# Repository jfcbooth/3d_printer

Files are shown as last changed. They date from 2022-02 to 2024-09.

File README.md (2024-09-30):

# 3D PEEK Printer

All the project files are in the directories above. The graphic below sums up the project. If you are curious about how something was implemented, read the [final report here](reports/Capstone_Final_Report.pdf). I recommend first skimming it and looking at the images for a better idea of what the project entailed.

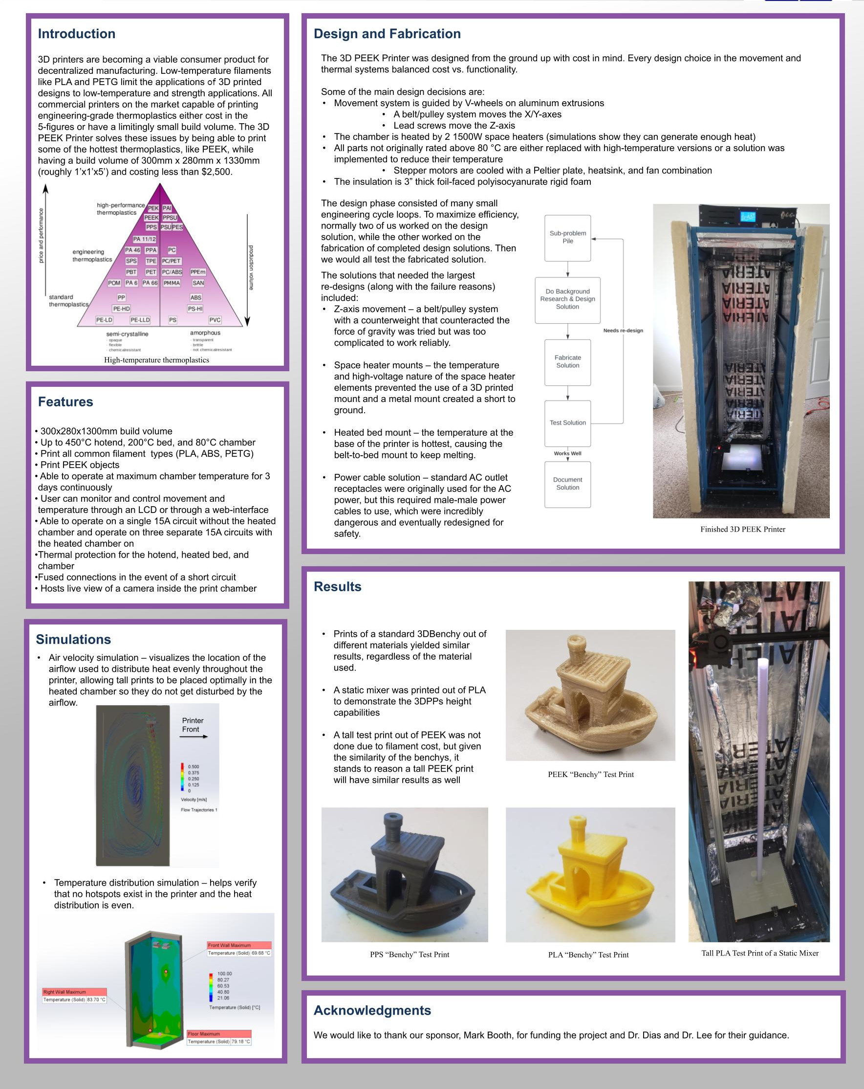
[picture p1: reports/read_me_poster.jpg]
Poster


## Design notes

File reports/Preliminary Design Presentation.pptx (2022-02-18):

## 3D Peek Printer

- Senior Capstone Design

## 3D Printing Technology

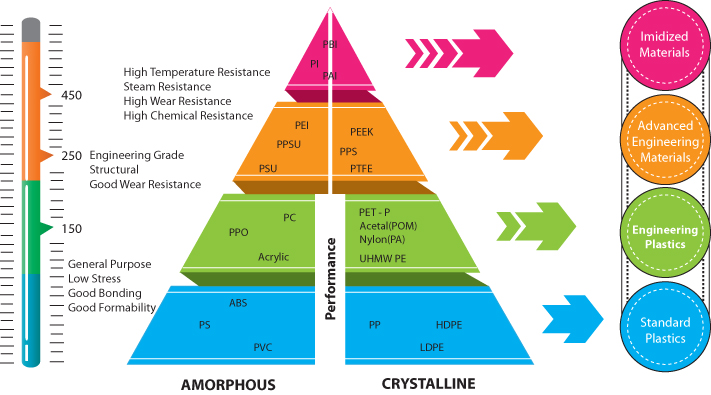
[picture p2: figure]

Source: https://www.cil.co.th/engineering-plastics/

- Pros
  - Low machine cost
  - Low per-unit print cost
  - Rapid Production
  - Low size footprint
  - Wide availability
- Cons
  - Dimensionally inaccurate
    - ±0.1mm vs ±0.005mm for CNC
  - Limited object size
  - Low strength
  - Low temperature

## Market Analysis

| Max Extruder Temp. (°C) | Max Bed Temp. (°C) | Max Chamber Temp. (°C) | Build Volume (mm³) | Price ($)
Average Commercial PEEK Printer | 490 | 193 | 165 | 5.01e7 | 61,000
Intamsys Funmat HT | 450 | 160 | 90 | 1.76e7 | 6,000
Aon-M2+ | 450 | 200 | 135 | 1.30e8 | 50,000
3DPP | 450 | 200 | 80 | 1.12e8 | 2,500

- Intamsys Funmat HT
  - 10x smaller build volume
  - Double price

- Aon-M2+
  - Similar build volume
  - 20x price

## Design Requirements

Functional Requirements
- Respond to movement commands in the X, Y, Z, and extruder directions
- Heat nozzle to 450 °C, bed to 200 °C, chamber to 80 °C
- Print all common filament types without heated chamber
- Can print PEEK/PSU object
- Print volume of 300x280x1330mm
- Operate at maximum chamber temperature for 3 days continuously
Usability Requirements
- System can operate on a local 20A breaker without heated chamber and with a heated chamber on 3 separate 20A circuits
- Will have thermal protection for the nozzle, heated bed, and chamber
- System will have fused connections in the event of a short

User Experience Requirements
- User can monitor and control temperature and movement locally through an LCD
- Through a web interface, the user can:
  - Control nozzle, bed, and chamber temp
  - Control X, Y, Z, and E movement
  - Send commands
  - Start, stop, and monitor prints
  - View print through real-time stream

## Initial Concept Generation

Cartesian system
Belt/pulley combination with counterweight for Z-axis
Fail-safe latches at top and bottom of printer to prevent bottoming-out
Mount motors outside heated chamber, cool other motors with Peltier Plates
Space heater heating element
Surrounded by insulation

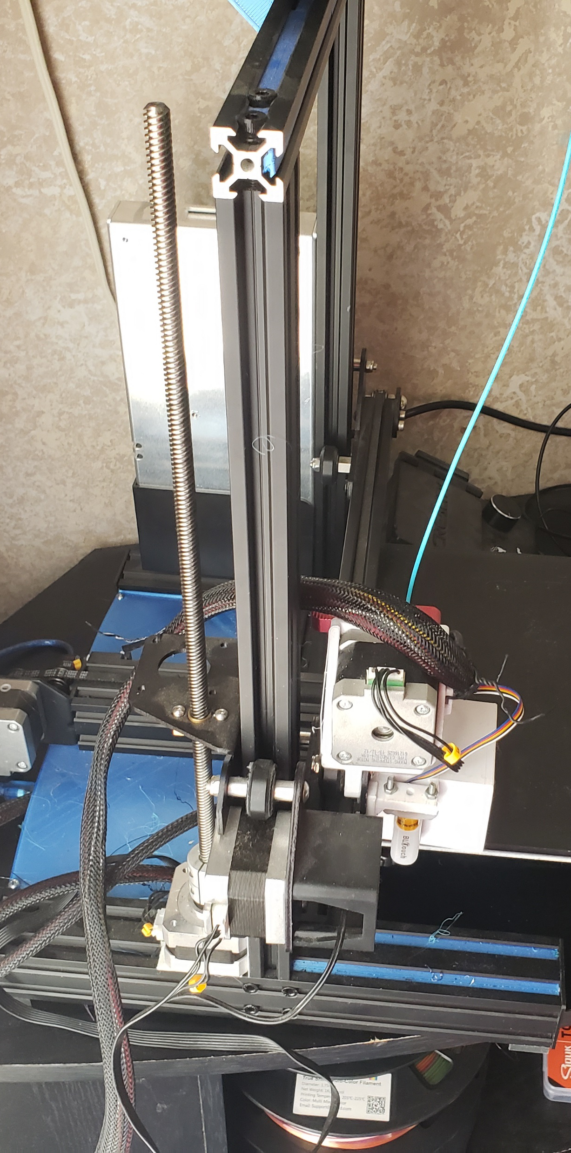
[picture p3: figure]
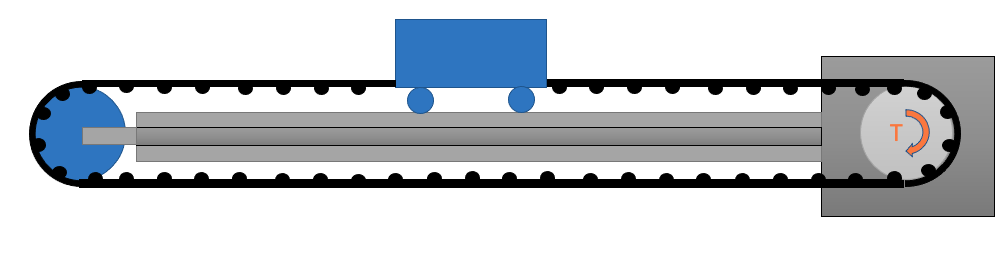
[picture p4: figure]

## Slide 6

Preliminary Thermal Analysis

Method 1

Method 2

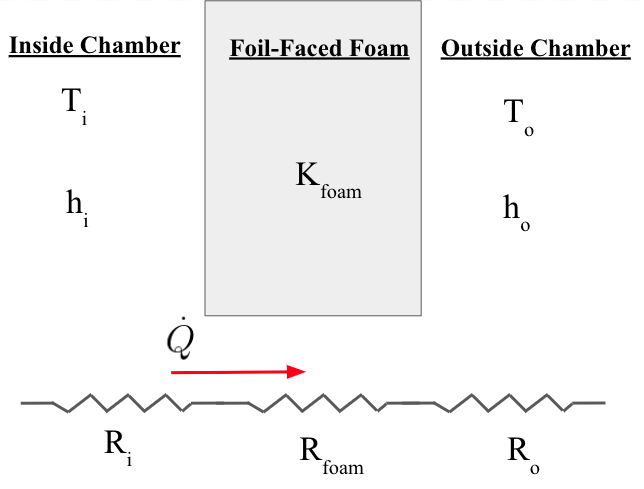
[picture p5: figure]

Pros
- Better Insulator (larger thickness)

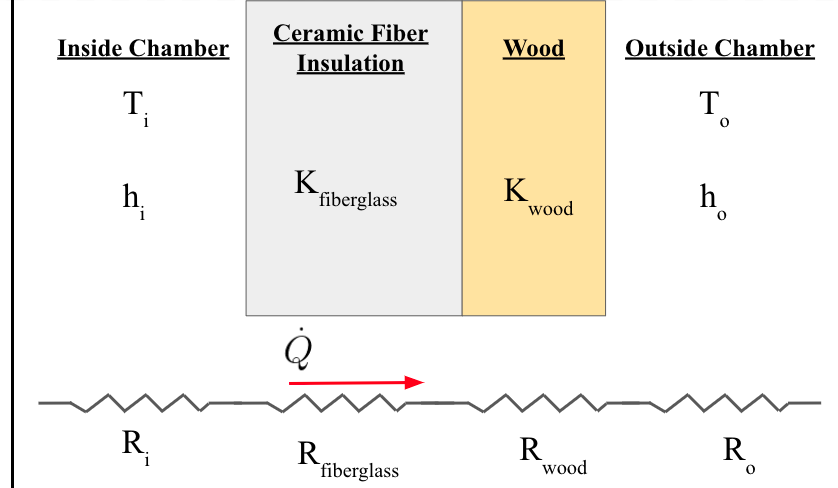
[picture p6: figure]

3”

1”

¼”

Cons
- Flaky
- Bulky

Pros
- Less Volume
- Sturdy
- Clean

Cons
- Worse Insulator

## Next Steps

- CAD Frame and Components
- Assemble movement system in frame
  - Build Z-axis movement mechanism
  - Design belt tensioning mechanisms
- Get working 3D printer without heated chamber
- Perform more complete thermal analysis on heating element

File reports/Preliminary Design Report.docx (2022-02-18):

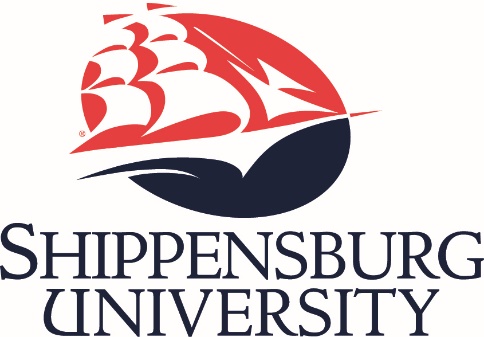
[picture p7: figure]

3D PEEK Printer

Preliminary Design Report

CMPE 499 – Engineering Design and Devlopment

Josh Booth, Dillon LaBonte, Caleb Coldsmith

Joao Dias, Sankook Lee

2/18/2022

# Abstract

In this report, we outline our plans to design and build a large (1’x1’x5’), high-temperature 3D printer capable of printing engineering-grade plastics, such as PEEK for $2,500. The 3D printing market is expanding rapidly due to the low cost of a 3D printer, fast production time, and low cost per print. Currently, most printers are only capable of printing weaker materials, due to the high temperatures and heated chamber required for the stronger plastics. The market is slowly expanding to stronger and higher temperature plastics, but with a very sharp increase in cost, or with a trade-off of a very small build volume, making these printers much less accessible to the common consumer. We look to remedy these problems by building a printer capable of printing PEEK with a build volume comparable to a $50,000 commercial printer at only $2,500. We hope to do this by combining a traditional, cheap printer movement system with high-temperature parts while employing novel solutions to counter the thermal issues and other issues spurred from the verticality of our print volume.

# 1. Problem Definition

## 1.1 Identification of Need or Opportunity

Over the past decade, 3D printing has become a popular manufacturing technique, due to its rapid per-unit production speed and low cost for both prints and the printer itself. However, traditional FDM printing is seldom used in projects requiring high structural strength or temperature due to the low printing temperatures (~200°C), and thus weak plastics available for use in most printers. As the industry grows, more companies have been designing commercial-grade, high-temperature printers that cost in the five figures, making them unobtainable to most hobbyists and consumers. In this report, we outline the steps needed to build a 3D printer capable of printing large items (1’x1’x5’) at high temperatures (400°C) while costing less than $2,500.

# 2. Basic Research

## 2.1 Existing Solutions

Below is a table of existing commercially available printers that can print PEEK. [1]

PEEK Printer Name | Build Volume (mm^3) | Max Extruder Temp (°C) | Max Bed Temp. (°C) | Max Chamber Temp. (°C) | Price
Intamsys Funmat HT | 1.76E+07 | 450 | 160 | 90 | 6,000
Tractus3D T850P | 3.14E+07 | 450 | 175 | 80 | 15,000
CreatBot PEEK-300 | 3.60E+07 | 500 | 200 | 120 | 17,000
Apium P220 | 4.77E+06 | 540 | 160 | 220 | 46,000
Zortrax Endureal | 3.60E+07 | 480 | 220 | 200 | 58,000
Roboze One+400 Xtreme | 1.65E+07 | 500 | 150 | N/A | 50,000
3ntr Spectral 30 | 2.70E+07 | 500 | 300 | 250 | 110,000
Essentium HSE 180 HT | 2.07E+08 | 550 | 100 | 200 | 149,000
3DGence Industry F340 | 2.65E+07 | 500 | 160 | 85 | 30,000
MiniFactory Ultra | 1.07E+07 | 480 | 250 | 250 | 50,000
Stratasys Fortus 450mc | 5.85E+07 | 450 | 250 | 350 | 160,000
Aon-M2+ | 1.30E+08 | 450 | 200 | 135 | 50,000
Averages | 5.01E+07 | 490 | 193 | 165 | 61,000
M3DD Printer | 1.12E+08 | 450 | 200 | 80 | 2,500

Table 1: Commercial PEEK Printers

All the commercial PEEK printers we could find have some tradeoff that made it unappealing. The most affordable printer, the Intamsys Funmat HT, has a build volume 10x smaller than ours at double the price. The printer that was closest in build volume to ours costs $50,000, making it far from affordable. We believe we are striking a middle-ground no other company has touched as of yet.

## 2.2 Market Analysis

In 2018, the 3D printing industry was worth 1.53 billion. By 2026, it is predicted to more than double to 3.78 billion. [2] While printer software and related services make up part of that, the printers themselves account for half the market. 3D printing is expanding into even the largest of industries, such as medical, automotive, and oil (which is our focus). [3] As shown by the large number of companies that are trying to expand into printing high-temperature plastics, printing PEEK and similar plastics has a promising future since it overcomes a lot of the strength and temperature shortcomings of lower-temperature plastics.

# 3. Design Requirements

## 3.1 Functionality Requirements

- The system should respond to movement commands in the X, Y, Z, and Extruder directions
- The system should be able to heat nozzle up to 450°C, bed up to 200°C, and chamber up to 80°C
- The system should be able to print all common filament types (PLA, ABS, PETG) with and without the heated chamber
- The system should be able to print PEEK and PSU objects
- The system should have a total usable print volume of 300x280x1330mm
- The system should be able to operate at the maximum chamber temperature for at least 3 days continuously without overheating or having part failure

## 3.2 Usability Requirements

- The system should be able to operate on a local 20A breaker without the heated chamber and with the heated chamber on three separate 20A circuits
- The system will have thermal protection for the hotend, heated bed, and chamber
- The system will have fused connections in the event of a short circuit

## 3.3 User Experience Requirements

- Users can monitor and control the temperature and movement of the system locally through the LCD
- Through a web interface, the user can:
- Control nozzle, bed, and chamber temperature
- Control X, Y, Z, and E movement
- Send commands
- Start, Stop, and monitor prints
- View print through real-time system

# 4. Initial Concept Generation

## 4.1 Frame

For a frame, aluminum extrusions are the de-facto standard for 3D printing frames due to their structural rigidity, low cost, and high functionality. We chose aluminum frames for the movement system and any structural pieces needed in a traditional FDM 3D printer. For the chamber frame, we chose to use a server rack. We found a server rack out-competed aluminum extrusions considering the overall size and mounting ease versus cost. This is a piece that would be trivial to replace given the required critical dimensions if another unit needed to be manufactured. The server rack will have insulation mounted to the outside of it and will provide a structural foundation for mounting our aluminum extrusion-based movement system.

## 4.2 Movement System

To move the hotend around the build volume, we are using a cartesian movement system with a pulley/belt combination. A coreXY printer would require an assembly the size of the bed volume to move through the entire print volume. This drastically increases complexity and would leave no room for auxiliary components like the heating elements. A delta printer would work in theory, but we will lose a lot of our build volume because of the circular build platform. For the cartesian design, the X and Y axes are easy to design and build as they fall within the typical sizes. However, the Z-axis requires a lot of engineering due to its unorthodox size. Most cartesian printers use a lead screw since it is sturdy, cost-effective, and self-locking in the event of power loss. If we were to use this method, we would need a 5’ lead screw, which would bend in the middle, no matter how perfectly the screw is made. To eliminate the lead screw, we want to use the most common Z-movement system for delta printers: a pulley/belt combination. However, this has its issues. It’s not as cheap, will require more motor torque to move if our X-carriage gets too heavy, and the X-carriage will fall in the event of power loss. To solve these issues, we plan to add a counterweight to reduce the amount of power needed to move the X-carriage and to stop the X-carriage from dropping in a power-loss event. We also plan to add spring-loaded fail-closed switches to the top and bottom to catch the X-carriage to prevent it from bottoming or topping out.

## 4.3 Computing

For the intelligence of our printer, we chose an SKR 2 Turbo due to its high ability to be customized along with TMC2099 stepper motors. They can drive 2A, which is the maximum drive current for our SKR 2. The SKR 2 allows us to connect to OctoPrint to monitor prints through a web interface and connect an LCD for local control and monitoring, per our design requirements. We plan on running Marlin firmware since it is open-source, highly customizable, and supports thermal protection. We are also going to host OctoPrint on a RaspberryPi running OctoPi, with custom software to run our chamber thermal protection, since Marlin’s chamber thermal protection may not cover our complex-use scenarios, such as someone opening the chamber during a print. This will cause a drop in the chamber temperature, which Marlin would register as an error and stop the print, but the act of opening the chamber itself isn’t a cause for triggering the thermal protection.

## 4.4 Heating System

The nozzle and bed heating elements by themselves will raise the internal temperature of the printer above ambient, but an additional heating element is needed to raise the chamber temperature to the level required to print PEEK. We are currently looking at using household space heater elements, as they only get up to between 120°C-200°C for safety reasons, which would be our ideal temperature. However, we have concerns about the safety of their construction and need to make sure they can get the entire chamber temperature to 80°C. Our preliminary anecdotal tests show that they should meet the temperature requirements, but we aren’t settled on a heating element until we finish our complete thermal analysis. To contain the heat, we are looking at two different options for insulation. The first option is foil-faced polyisocyanurate rigid foam insulation, as it has a similar thermal conductivity coefficient to air [4] [5]. However, this insulation not only is very bulky, but flakes off with time, which will reduce print adhesion, and thus print quality. The second option is a fiberglass and wood insulation combination, as it would solve our flaking issue and be much slimmer. However, while we know that the fiberglass/wood insulation will have a high rate of heat transfer than the foam, we haven’t determined if choosing a more heavy-duty heating element would allow this alternative insulation method to work. See a more complete thermal analysis in section 5.3.

## 4.5 Thermal Management

While we want our chamber to be hot, certain components should not get hot, such as the stepper motors. To cool our stepper motors, we are mounting the possible ones, such as our Z and Y motors, outside of the build chamber and only have the shaft inside the chamber. This would allow us to keep those stepper motors at ambient temperature. The X and the E motors can’t be located outside the heated chamber, so we are using Peltier Plates to cool those motors. The cold side would be on the motor, and the hot side would be attached to a heatsink and fan to reduce the temperature, whose heat would add to the chamber temperature. Additionally, the temperature of the camera that monitors the print should be thermally managed. It doesn’t get anywhere near as hot as the motors, but to reduce the temperature, we surrounded the camera in aluminum tape to minimize the freshly heated air warming up the camera.

# 5. Preliminary Analysis

## 5.1 Initial Power Analysis

We plan on splitting up the power into three circuits to satisfy the design requirements. We are having two A/C circuits for our chamber heating elements, and then a 3rd A/C circuit for all other components. The heating elements of the space heaters we are planning on using are 1500W each. At 120V, this yields (1500W)/(120V)=12.5A per space heater, keeping us below our 20A breaker design requirement. We are assuming to use 2 space heaters, although we won’t be able to know for sure until we complete full the thermal analysis.

For the DC components, we need to pick an adequate power supply. Below is a table of the power draw requirement estimates for each component. For the voltage conversions, we are assuming a worst-case efficiency of 70% for our buck converters. [6] These currents are also over-estimates assuming max-load on each component. We won’t be able to test each unit for the actual power draw (such as the raspberry pi and SKR board until we can power them up). We are only able to off manufacturer specifications and tests done by 3rd parties.

Part | Voltage/unit | Amperage/unit (with conversion efficiency included) | Quantity | Total Amperage Used
Name 17 2A motor | 24 | 2 | 3 | 4
Nema 17 motor (high power) | 24 | 0.58 | 2 | 1.74
SKR Board | 24 | 0.5 | 1 | 0.5
Heater Cartidge | 24 | 2.08 [7] | 1 | 2.08
Space heater fans | 12 | 0.33 | 2 | 0.858
RPi | 5 | 0.4 [8] | 1 | 0.52
LED Strip | 5 | 0.06 [9] | 5 | 0.39
Peltier Plates (@ 5V) | 5 | 1.5 [10] | 2 | 3.9
Bed heater element (AC power) | AC | 4.1 | 1 | 4.1
| | | Summation: | 18.088 A

Table 2: Power Analysis

We are using 18.088A for the primary AC connection. We need 13.99A for our power supply since the heated bed doesn’t contribute to the load on the power supply. The power supply we chose was a Meanwell 24V/21A power supply. This gives us breathing room, so we aren’t always stressing our power supply and the price difference between a 24V/15A and 24V/21A power supply was negligible.

## 5.2 Initial Movement Analysis

As mentioned in our initial concept generation, We plan to use 3 separate belt/pulley systems to control our 3 axes of motion. Each system would require a stepper motor to move the bed or carriages. By creating a free body diagram of the carriage, we will be able to find the needed torque of the motor in the x-direction.

Variable | Value | Units | Name
mc | 0.297 | kg | Mass of the carriage
rm | 0.0047 | m | Radius of the Motor
amax | 0.5 | m/s² | Maximum acceleration
µ | 0.0015 [11] | N/A | Coefficient of friction
g | 9.81 | m/s² | Gravitational acceleration

Table 3: Movement Values

x-direction movement system Free Body Diagram

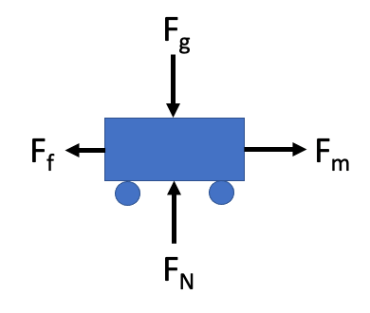
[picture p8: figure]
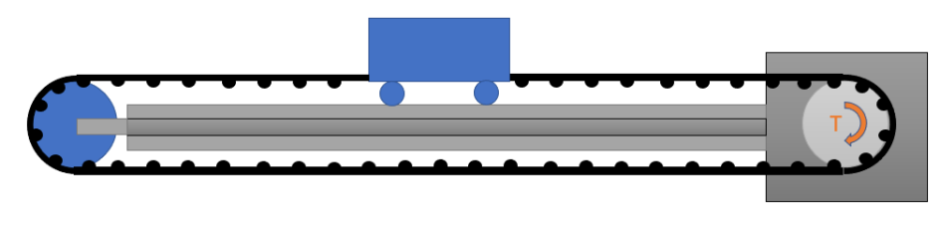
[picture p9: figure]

Where F_g =Weight of the Carriage=m_c *g=0.297*9.81=2.62 N

∑F_y =0=F_N -F_g F_N =Normal Force=F_g =2.62 N

F_f =Force of Friction=μ*F_N =0.0015*2.62=3.93*10^(-3) N

∑F_x =m_c *a_(max) =0.297*0.5=0.149=F_m -F_f F_m =0.1485+3.93*10^(-3) =0.152 N

T_m =r_m *F_m =0.0047*0.152=0.714 Ncm Required Torque by our Stepper Motor

While the calculation for required torque is straightforward, a much more in-depth analysis of our stepper motors needs to take place to calculate the amount of torque our stepper motors can provide at the desired speed and acceleration of our carriage. Variables such as max rotational speed, number of microsteps per full step, belt tooth and pitch sizes, and motor efficiency all need to be taken into account. Similar calculations will also need to take place in determining the required torque by our stepper motor in the y and z-direction as well.

## 5.3 Initial Thermal Analysis

For our initial thermal analysis, we had two ideas for our insulation types, as mentioned in section 4.4, the foil-faced polyisocyanurate rigid foam insulation and the fiberglass/wood combination. We want to determine which method better retains heat, even though we would prefer the fiberglass/wood insulation due to the flaking and bulkiness of the foil-faced foam insulation. To do this, we calculated the heat transfer rate for each type of insulation for a single side of the chamber. This will let us know which insulation type is more effective.

We assumed the outside ambient temperature was 72°F, or 22.2°C, and the inside temperature was 80°C, our maximum chamber temperature as listed in the design requirements. We also estimated our convection heat transfer coefficients, since it is dependent on the airflow, and we have not determined how the air will flow in our system yet. This analysis is simply to show the difference in the effectiveness of our two methods of insulation.

Variable | Value | Units | Name
Ti | 80 | C | Temperature inside
To | 22.2 | C | Temperature outside
Cheight | 1.651 | m | Chamber height
Cwidth | 0.535 | m | Chamber width
Clength | 0.648 | m | Chamber length
A | 1.069 | m² | Cross-sectional area
Lfoam | 0.0762 | m | Foam depth
Lfiberglass | 0.0254 | m | Fiberglass depth
Lwood | 0.00635 | m | Wood depth
ho | 12 [12] | W/m²⋅K | Heat transfer coefficient outside
hi | 120 [12] | W/m²⋅K | Heat transfer coefficient inside
Kfoam | 0.026 [5] | W/m⋅K | Foam thermal conductivity
Kfiberglass | 0.0316 [13] | W/m⋅K | Fiberglass thermal conductivity
Kwood | 0.12 [14] | W/m⋅K | Wood thermal conductivity

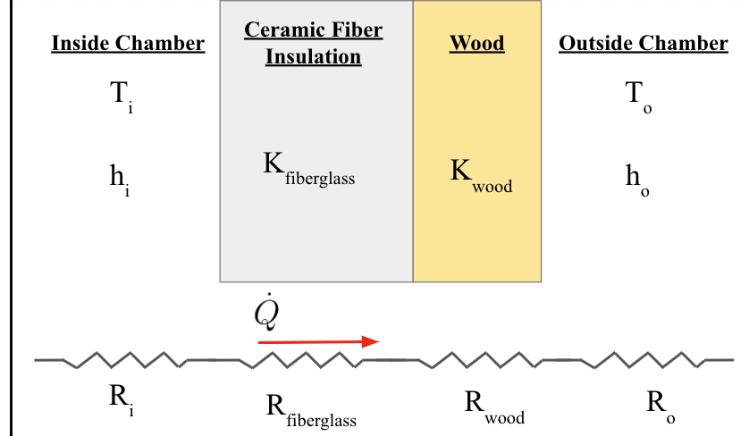
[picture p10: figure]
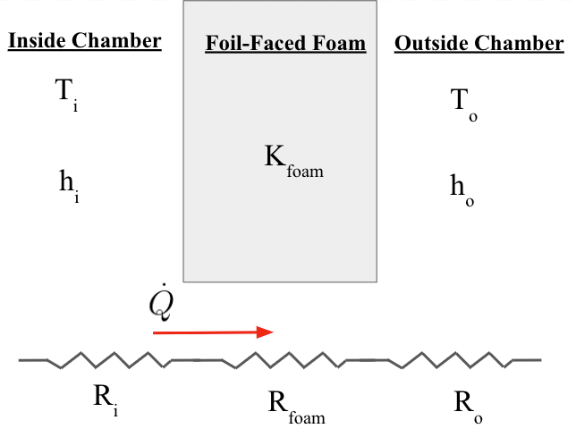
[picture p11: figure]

Table 4: Thermal Values

The heat transfer rate of the foil-faced foam is:

R_(total_foam) = R_i +R_(foam) +R_o where R_i = 1/(h_i *A) , R_(foam) = (L_(foam))/(K_(foam) *A) , and R_o = 1/(h_o *A)

Q_(foam) =(T_i -T_o)/(R_(total))=20.45 W

The heat transfer rate of the fiberglass/wood is:

R_(total_fiberglass) = R_i +R_(foam) +R_o

where R_i = 1/(h_i *A) , R_(fiberglass) = (L_(fiberglass))/(K_(fiberglass) *A) , R_(wood) = (L_(wood))/(K_(wood) *A) , and R_o = 1/(h_o *A)

Q_(fiberglass) =(T_i -T_o)/(R_(total))=65.17 W

By using the thermal resistivity method of analysis, we were able to compare the effectiveness of each method of insulation. The heat transfer rate for the foil-faced foam was lower than the one for the fiberglass/wood, making it a better insulator. This is not surprising, as the foil-faced foam has a much larger thickness, resulting in a lower heat transfer rate. To determine if we need to use the foil-faced foam, we need a more complete thermal analysis before we can rule out using the fiberglass/wood combination, since this insulation combination may still work with our current heating element choice. Additionally, we could also choose a larger heating element if necessary. Although the foil-faced foam is a better insulator, it still has the flaking and bulk problems listed in section 4.4, incentivizing us to continue more in-depth thermal analysis until we are certain we have to use the foam.

# 6. Schedule

Week | Date | Timeline
Week 1 | 01/18 – 01/21 | Capstone introduction
Week 2 | 01/24 – 01/28 | Project selection
Week 3 | 01/31 – 02/04 | Part selection for movement system CAD all parts for movement system for future analysis Setup project requirements Initial budget
Week 4 | 02/07 – 02/11 | Continue CADIng all parts for the movement system Design case for mounting electronics Determine a Z-axis mechanism for movement
Week 5 | 02/14 – 02/18 | Design Y tensioning mechanism Install movement system into frame Preliminary report/presentation
Week 6 | 02/21 – 02/25 | Make movement system work Install electronics/ run wiring
Week 7 | 02/28 – 03/04 | Debug movement system Design/replace parts that need it
Week 8 | 03/07 – 03/11 | Calibrate printer w/o heated chamber Start thermal analysis
Week 9 | 03/14 – 03/18 | Determine thermal materials and order it Critical design report/presentation
Week 10 | 03/21 – 03/25 | Install thermal materials and get the printer up to temperature
Week 11 | 03/28 – 04/01 | Run test prints at max temperatures
Week 12 | 04/04 – 04/08 | Debug thermal/electrical issues
Week 13 | 04/11 – 04/15 | Debug thermal/electrical issues Create final report
Week 14 | 04/18 – 04/22 | Work on final report and presentation
Week 15 | 04/25 – 04/29 | Finish final report/presentation and dry run presentation

Table 4: Schedule

# 7. Preliminary Budget

Name | Cost | Quantity | Name | Cost | Quantity
SKR 2 | 49.99 | 1 | Garolite | 15.95 | 2
Rpi | 34.99 | 1 | Heated bed | 159.99 | 1
Buck Converter | 9.99 | 1 | wires | 20 | 2
LCD | 16.95 | 1 | Leadscrews | 55 | 2
SSR | 10.49 | 3 | anti-backlash nuts | 10.98 | 1
Fuses | 8.47 | 1 | Insulation | 100 | 1
Power Supply | 35.99 | 1 | Kaolin cloth | 20 | 1
Aluminum Extrusions | 23.25 | 2 | High temp belt | 11.99 | 1
High power motor | 13.99 | 2 | high temp wheels | 21.99 | 1
Low power motor | 10.99 | 2 | breaker | 9.99 | 1
Extruder | 12.99 | 1 | outlets | 9.99 | 1
Peltier Plates + heatsinks | 31.35 | | switches | 9.99 | 1
24V fans | 11.99 | 1 | sheet metal | 30 | 1
pi camera + 6ft cable | 15.04 | | frame | 75 | 1
End stops | 9.99 | 2 | bowden setup | 19.99 | 1
Mosquito hotend | 149.99 | 1 | printed parts (estimate) | 100 | 1
mosquito thermistor | 69.99 | 1 | wifi adapter | 10.55 | 1
heater cartridge | 15.99 | 1 | BLTouch | 40.26 | 1
led strip | 11.92 | 1 | capacitors | 11.65 | 1

Table 5: Preliminary Budget

Total cost: 1,701.43

With a 30% price increase, the total cost is $2,211.86

# 8. Conclusions and Next Steps

The next steps are to continue following our schedule. In the coming weeks, we will build our movement system and verify functionality as a 3D printer without a heated chamber. We hope to have this done before the critical design report is due. After that, we will be able to finish our full thermal analysis (if we haven’t already done so by then) after we have determined our movement systems and begin designing our heated chamber. Of course, when building our movement system, we are selecting components that can withstand temperatures of 80°C. At the time of writing, we are perfecting the design of our Z-movement system, overcoming the obstacles of a very tall build volume.

# 9. Bibliography

## References

[1] C. Schwaar, "PEEK 3D Printers - The Ultimate Guide", all3dp.com, 2022. [Online]. Available: https://all3dp.com/1/peek-3d-printer/. [Accessed: 14- Feb- 2022].

[2] "Global 3D printing material market size 2026 | Statista", Statista, 2022. [Online]. Available: https://www.statista.com/statistics/590113/worldwide-market-for-3d-printing/. [Accessed: 14- Feb- 2022].

[3] T. Novicio, "Yahoo is part of the Yahoo family of brands", Yahoo.com, 2022. [Online]. Available: https://www.yahoo.com/video/10-biggest-industries-world-2021-150703784.html. [Accessed: 14- Feb- 2022].

[4] "Air - Thermal Conductivity vs. Temperature and Pressure", Engineeringtoolbox.com, 2022. [Online]. Available: https://www.engineeringtoolbox.com/air-properties-viscosity-conductivity-heat-capacity-d_1509.html. [Accessed: 15- Feb- 2022].

[5] "AP™ Foil-Faced POLYISOCYANURATE CONTINUOUS INSULATION", Jm.com, 2022. [Online]. Available: https://www.jm.com/content/dam/jm/global/en/building-insulation/Files/BI%20Data%20Sheets/Resi%20and%20Commercial/BID-0151-AP-FoilFaced-DS.pdf. [Accessed: 15- Feb- 2022].

[6] J. Farr, "Review of DC to DC buck converter based on LM2596", Joe's Hobby Electronics, 2022. [Online]. Available: https://www.hobbyelectronics.net/review_dctodcmodule.html. [Accessed: 14- Feb- 2022].

[7] "50W Heater Cartridge", Slice Engineering, 2022. [Online]. Available: https://www.sliceengineering.com/products/50w-heater-cartridge. [Accessed: 14- Feb- 2022].

[8] S. Shovon, "Raspberry Pi 3 Power Requirements", Linuxhint.com, 2022. [Online]. Available: https://linuxhint.com/raspberry_pi_3_power_requirements/. [Accessed: 15- Feb- 2022].

[9] L. Ada, "RGB LED Strips", Adafruit Learning System, 2022. [Online]. Available: https://learn.adafruit.com/rgb-led-strips/current-draw. [Accessed: 14- Feb- 2022].

[10] "PRODUCT SPECIFICATION OF THERMOELECTRIC COOLING MODULE", Cdn-reichelt.de, 2022. [Online]. Available: https://cdn-reichelt.de/documents/datenblatt/C800/TECB1.pdf. [Accessed: 14- Feb- 2022].

[11] M. Santora, "Bearing friction basics: A primer - Bearing Tips", Bearing Tips, 2022. [Online]. Available: https://www.bearingtips.com/bearing-friction-basics-primer/. [Accessed: 18- Feb- 2022].

[12] M. Malekan, A. Khosravi and M. El Haj Assad, "Parabolic trough solar collectors", sciencedirect.com, 2022. [Online]. Available: https://www.sciencedirect.com/topics/engineering/convection-heat-transfer-coefficient. [Accessed: 15- Feb- 2022].

[13] "Kaowool Blanket", Morganthermalceramics.com, 2022. [Online]. Available: https://www.morganthermalceramics.com/media/2975/5-14-205_kaowoolblankets_072018.pdf. [Accessed: 15- Feb- 2022].

[14] "Thermal Conductivity", Hyperphysics.phy-astr.gsu.edu, 2022. [Online]. Available: http://hyperphysics.phy-astr.gsu.edu/hbase/Tables/thrcn.html. [Accessed: 15- Feb- 2022].

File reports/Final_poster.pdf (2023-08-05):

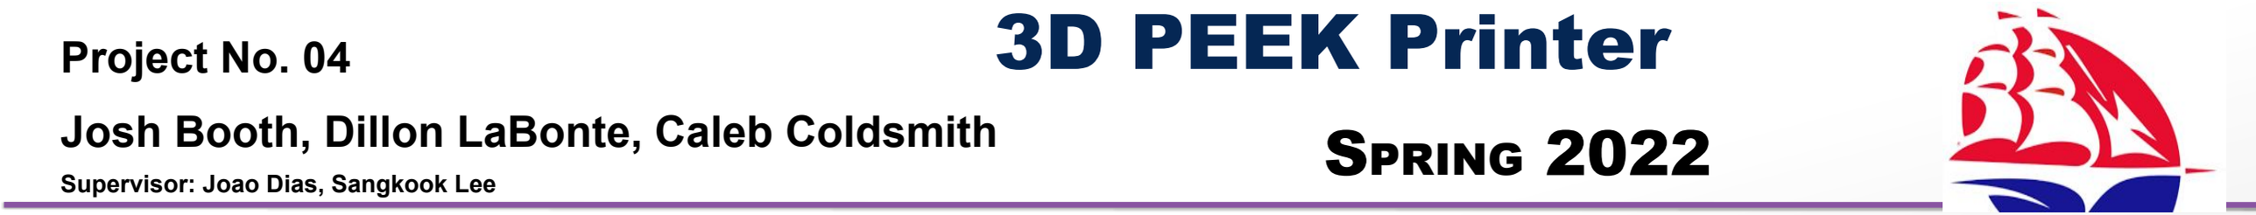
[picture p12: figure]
Project No. 04; Supervisor: Joao Dias, Sangkook Lee; 3D PEEK Printer; SPRING 2022

## Results

## Simulations

- Air velocity simulation – visualizes the location of the airflow used to distribute heat evenly throughout the | different materials yielded similar results, regardless of the material used.
printer, allowing tall prints to be placed optimally in the heated chamber so they do not get disturbed by the | • A static mixer was printed out of PLA to demonstrate the 3DPPs height capabilities • A tall test print out of PEEK was not done due to filament cost, but given the similarity of the benchys, it stands to reason a tall PEEK print will have similar results as well

airflow.

## Introduction

3D printers are becoming a viable consumer product for decentralized manufacturing. Low-temperature filaments like PLA and PETG limit the applications 3D printed designs to low-temperature and strength applications. All commercial printers on the market capable of printing engineering-grade thermoplastics either cost in the 5-figures or have a limitingly small build volume. The 3D PEEK Printer solves these issues by being able to print some of the hottest thermoplastics, like PEEK, while having a build volume of 300mm x 280mm x 1330mm (roughly 1’x1’x5’) and costing less than $2,500.

## Design and Fabrication

# Josh Booth, Dillon LaBonte, Caleb Coldsmith

## Acknowledgments

We would like to thank our sponsor, Mark Booth, for funding the project and Dr. Dias and Dr. Lee for their guidance.

# Shippensburg University of Pennsylvania

# School of Engineering – Civil and Mechanical Engineering Department

## Features

- 300x280x1300mm build volume
- Up to 450°C hotend, 200°C bed, and 80°C chamber
- Print all common filament types (PLA, ABS, PETG)
- Print PEEK objects
- Able to operate at maximum chamber temperature for 3 days continuously
- User can monitor and control movement and temperature through an LCD or through a web-interface
- Able to operate on a single 15A circuit without the heated chamber and operate on three separate 15A circuits with the heated chamber on
•Thermal protection for the hotend, heated bed, and chamber
•Fused connections in the event of a short circuit
- Hosts live view of a camera inside the print chamber
- Temperature distribution simulation – helps verify that no hotspots exist in the printer and the heat distribution is even.

Finished 3D PEEK Printer

PLA “Benchy” Test Print

The 3D PEEK Printer was designed from the ground up with cost in mind. Every design choice in the movement and thermal systems balanced cost vs. functionality.

Some of the main design decisions are:
- Movement system is guided by V-wheels on aluminum extrusions
- A belt/pulley system moves the X/Y-axes
- Lead screws move the Z-axis
- The chamber is heated by 2 1500W space heaters (simulations show they can generate enough heat)
- All parts not originally rated above 80 °C are either replaced with high-temperature versions or a solution was implemented to reduce their temperature
- Stepper motors are cooled with a Peltier plate, heatsink, and fan combination
- The insulation is 3” thick foil-faced polyisocyanurate rigid foam

PEEK “Benchy” Test Print

Tall PLA Test Print of a Static Mixer

- Prints of a standard 3DBenchy out of

PPS “Benchy” Test Print

High-temperature thermoplastics

The design phase consisted of many small engineering cycle loops. To maximize efficiency, normally two of us worked on the design solution, while the other worked on the fabrication of completed design solutions. Then we would all test the fabricated solution.

The solutions that needed the largest re-designs (along with the failure reasons) included:
- Z-axis movement – a belt/pulley system with a counterweight that counteracted the force of gravity was tried but was too complicated to work reliably.
- Space heater mounts – the temperature and high-voltage nature of the space heater elements prevented the use of a 3D printed mount and a metal mount created a short to ground.
- Heated bed mount – the temperature at the base of the printer is hottest, causing the belt-to-bed mount to keep melting.
- Power cable solution – standard AC outlet receptacles were originally used for the AC power, but this required male-male power cables to use, which were incredibly dangerous and eventually redesigned for safety.

Printer
Front

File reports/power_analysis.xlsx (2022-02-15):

PEEK Printer Name | Build Volume (mm) | Max Extruder Temp | Max Bed Temp | Max Chamber Temp | Price
Intamsys Funmat HT | 260 x 260 x 260 | 450 | 160 | 90 | 6000 | 260 | 260 | 260 | 17576000
Tractus3D T850P | 280 x 280 x 400 | 450 | 175 | 80 | 15000 | 280 | 280 | 400 | 31360000
CreatBot PEEK-300 | 300 x 300 x 400 | 500 | 200 | 120 | 17000 | 300 | 300 | 400 | 36000000
Apium P220 | 205 x 155 x 150 | 540 | 160 | 220 | 46000 | 205 | 155 | 150 | 4766250
Zortrax Endureal | 300 x 400 x 300 | 480 | 220 | 200 | 58000 | 300 | 400 | 300 | 36000000
Roboze One+400 Xtreme | 300 x 250 x 220 | 500 | 150 | N/A | 50000 | 300 | 250 | 220 | 16500000
3ntr Spectral 30 | 300 x 300 x 300 | 500 | 300 | 250 | 110000 | 300 | 300 | 300 | 27000000
Essentium HSE 180 HT | 690 x 500 x 600 | 550 | 100 | 200 | 149000 | 690 | 500 | 600 | 207000000
3DGence Industry F340 | 260 x 300 x 340 | 500 | 160 | 85 | 30000 | 260 | 300 | 340 | 26520000
MiniFactory Ultra | 330 x 180 x 180 | 480 | 250 | 250 | 50000 | 330 | 180 | 180 | 10692000
Stratasys Fortus 450mc | 406 x 355 x 406 | 450 | 250 | 350 | 160000 | 406 | 355 | 406 | 58516780
Aon-M2+ | 450 x 450 x 640 | 500 | 200 | 135 | 50000 | 450 | 450 | 640 | 129600000
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

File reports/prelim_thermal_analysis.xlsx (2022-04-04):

Variable | Value | Unit | Note
T_i | 80 | C
T_o | 22.2 | C
Height | 1.651 | m
Width | 0.534924 | m
Length | 0.6477 | m
A | 1.0693527 | m^2 | Cross-sectional area
h_o | 12 |  | Outside heat transfer coefficient
h_i | 120 |  | Inside heat transfer coefficient
R_i | 0.00779287632
R_o | 0.0779287632 |  |  |  |  |  |  | K_fiberglass determination |  | At X = 100 | 0.0316
 |  |  |  |  |  |  |  | Temp | Thermal conductivity
 |  |  |  |  |  |  |  | 260 | 0.06
Foil faced foam Analysis |  |  |  | Fiberglass/wood analysis |  |  |  | 538 | 0.12
K_foam | 0.026 | W/mK | https://www.jm.com/content/dam/jm/global/en/building-insulation/Files/BI%20Data%20Sheets/Resi%20and%20Commercial/BID-0151-AP-FoilFaced-DS.pdf | K_fiberglass | 0.0316 | W/mK | https://www.morganthermalceramics.com/media/2975/5-14-205_kaowoolblankets_072018.pdf | 816 | 0.21
L_foam | 0.0762 | m |  | K_wood | 0.12 | W/mK | http://hyperphysics.phy-astr.gsu.edu/hbase/Tables/thrcn.html | 1093 | 0.3
R_foam | 2.740694656 |  |  | L_fiberglass | 0.0254 | m
 |  |  |  | L_wood | 0.00635 | m
R_total | 2.826416296 |  |  | R_fiberglass | 0.7516673108
Q | 20.44992455 |  |  | R_wood | 0.04948476463
 |  |  |  | R_total | 0.886873715
 |  |  |  | Q | 65.17275123

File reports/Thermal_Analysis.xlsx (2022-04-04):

Variable
T_i | 80 | Left/Right Wall |  |  |  |  | Front/Back Wall |  |  |  | Top/Bottom Wall
T_o | 22.2 | A_LR | 1.069 | X 2 |  |  | A_FB | 0.883 | X 2 |  | A_TB | 0.346 | X 2
Height | 1.651 | R_i | 0.1676187773 | 0.3352375545 |  |  | R_i | 0.2029572089 | 0.4059144179 |  | R_i | 0.5173419051 | 1.03468381
Width | 0.535 | R_wall | 35.96712148 | 71.93424295 | *t |  | R_wall | 43.54993341 | 87.09986682 | *t | R_wall | 111.0096342 | 222.0192684 | *t
Length | 0.648 | R_o | 0.0779287632 | 0.1558575264 |  |  | R_o | 0.09435818906 | 0.1887163781 |  | R_o | 0.2405208741 | 0.4810417481
h_i | 5.579 | R_LR | 0.4910950809 | + 71.934243t |  |  | R_FB | 0.297315398 | + 87.0998668t |  | R_TB | 0.7578627792 | + 222.019268t
h_o | 12
k_foam | 0.026
K_fiberglass | 0.0316 |  |  |  |  | R_total | 1.546273258 | + | 381.0533781 | *t
K_wood | 0.12
 |  |  |  |  |  | R_total | 1.546273 + 381.0533781 * t
 |  | Q | t (m)
 |  | 200 | -0.003299466072
 |  | 400 | -0.003678678036
 |  | 600 | -0.003805082024
 |  | 800 | -0.003868284018
 |  | 1000 | -0.003906205214
 |  | 1200 | -0.003931486012
 |  | 1400 | -0.003949543725
 |  | 1600 | -0.003963087009
 |  | 1800 | -0.003973620675
 |  | 2000 | -0.003982047607
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

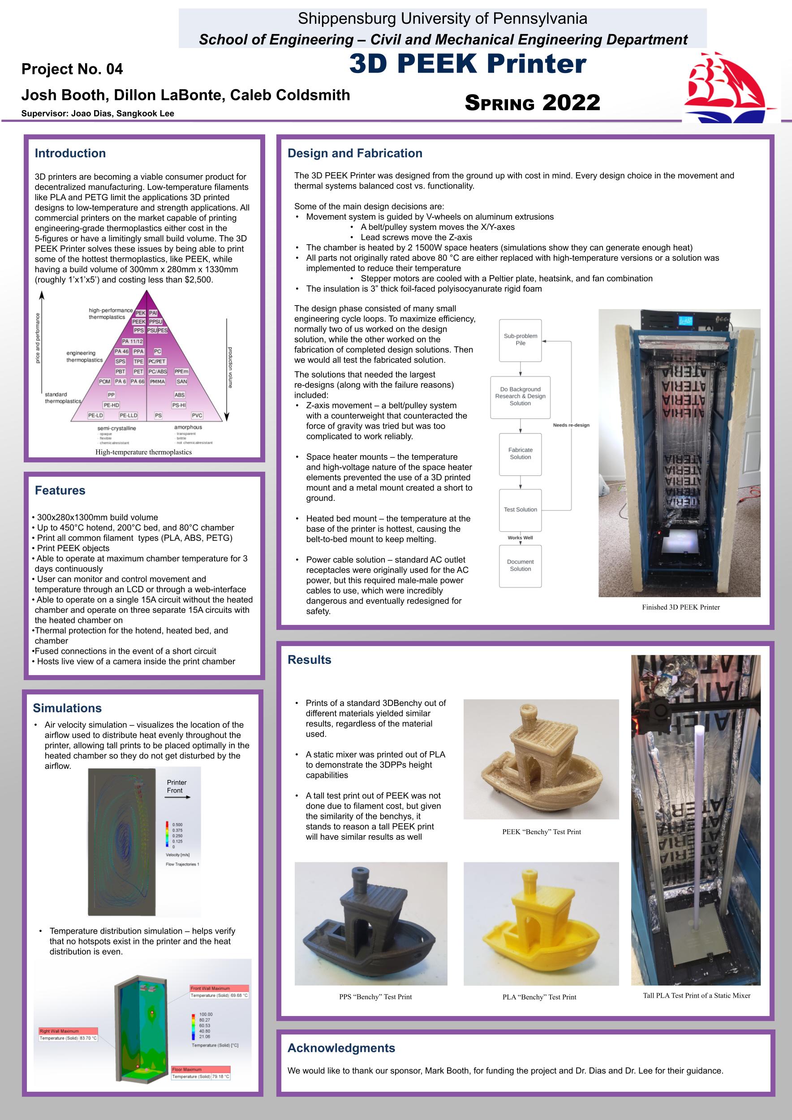
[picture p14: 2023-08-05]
reports/Final_poster.jpg

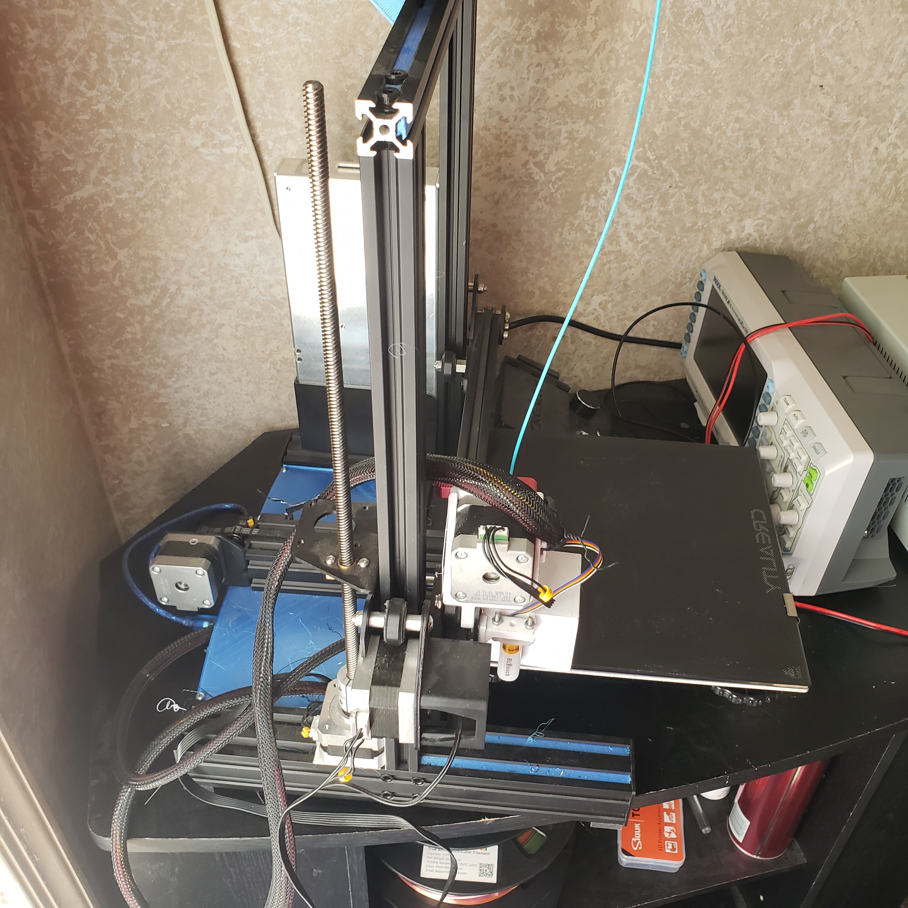
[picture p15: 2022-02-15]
reports/zaxis.jpg

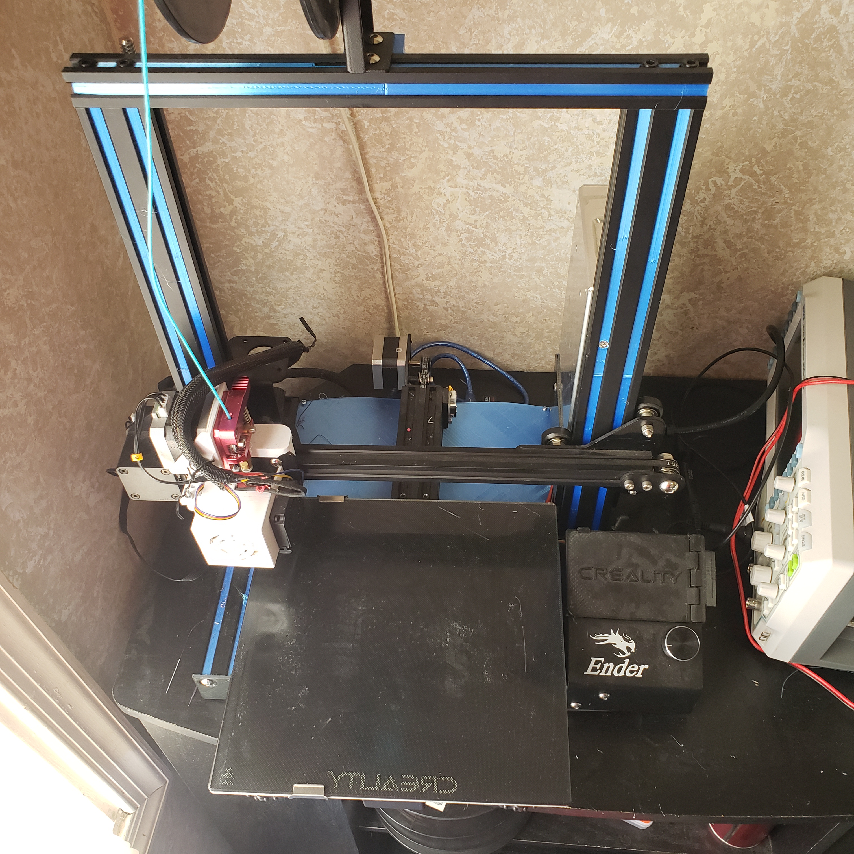
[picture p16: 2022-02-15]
reports/cartesian.jpg

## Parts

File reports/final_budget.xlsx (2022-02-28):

Name | Cost | Quantity | Notes | Link
SKR 2 | 49.99 | 1 |  | https://www.amazon.com/BIGTREETECH-Control-Upgrade-Motherboard-Compitable/dp/B0943WVM5B
Rpi | 34.99 | 1
Buck Converter | 9.99 | 1 |  | https://www.amazon.com/Queta-Converter-Efficiency-Stabilizer-Transformer/dp/B08G4GYNL6
LCD | 16.95 | 1
SSR | 10.49 | 3 |  | https://www.amazon.com/MYSWEETY-SSR-40DA-Single-Semi-Conductor-24-380V/dp/B073B4R4LS
Fuses | 8.47 | 1
Power Supply | 35.99 | 1 |  | https://www.amazon.com/Adjustable-DROK-110V-220V-Switching-Transformer/dp/B08GFSVHLS
Aluminum Extrusions | 23.25 | 2 |  | https://www.amazon.com/80-20-20-2020-T-Slotted-Extrusion/dp/B001F0I3G2
High power motor | 13.99 | 2 |  | https://www.amazon.com/STEPPERONLINE-Stepper-Bipolar-Connector-compatible/dp/B00PNEQKC0
Low power motor | 10.99 | 2 |  | https://www.amazon.com/Twotrees-Stepper-17HS4401-Connector-Printer/dp/B07THK76QQ
Extruder | 12.99 | 1 |  | https://www.amazon.com/Creality-Upgraded-Extruder-Capricorn-Pneumatic/dp/B089NFCK73
Peltier Plates + heatsinks | 31.35
24V fans | 11.99 | 1 |  | https://www.amazon.com/WINSINN-Upgrade-Hydraulic-Bearing-CR-10S/dp/B0757RPCN9
pi camera + 6ft cable | 15.04
End stops | 9.99 | 2 |  | https://www.amazon.com/OIIKI-Switch-Printer-Control-Ender-3/dp/B08HYXWGCC
Mosquito hotend | 149.99 | 1 |  | https://www.sliceengineering.com/products/the-mosquito-hotend
mosquito thermistor | 69.99 | 1 |  | https://www.sliceengineering.com/collections/accessories/products/thermistor-high-temperature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
heater cartridge | 15.99 | 1 |  | https://www.sliceengineering.com/collections/accessories/products/50w-heater-cartridge
led strip | 11.92 | 1
Garolite | 15.95 | 2 |  | https://www.amazon.com/Gizmo-Dorks-Preapplied-Laminated-Adhesive/dp/B07GSJSDWR
Heated bed | 159.99 | 1 |  | https://e3d-online.com/products/high-temperature-heated-beds
wires | 20 | 2 |  | https://www.amazon.com/Hygoo-Flexible-Silicone-Stranded-Copper/dp/B07C314Y5H
Lead screws | 55 | 2
anti-backlash nuts | 10.98 | 1 |  | https://www.amazon.com/Backlash-Elimination-Upgrade-Tornado-Threaded/dp/B08LZ1V56T
Insulation | 300 | 1
Kaolin cloth | 20 | 1
High temp belt | 11.99 | 1 |  | https://www.amazon.com/Upgrade-Non-Slip-Version-Printer-Printers/dp/B08R93QQ8Z
high temp wheels | 21.99 | 1 |  | https://www.amazon.com/Pack%E3%80%913D-Polycarbonate-Creality-Artillery-Accessories/dp/B08MX47WG8
breaker | 9.99 | 1
outlets | 9.99 | 1
switches | 9.99 | 1
sheet metal | 30 | 1 |  | Lowes
frame | 100 | 1
bowden setup | 19.99 | 1
printed parts (estimate) | 100 | 1
wifi adapter | 10.55 | 1
bltouch | 40.26 | 1
capacitors | 11.65 | 1
hardware | 100 | 1
test prints filament (engineering plastics) | 200 | 1
gt2 pulley | 10.9 | 1
magnets + v-pulley + copper buckle + wire | 69.92 | 1
scale + 80mm fans + gt2 idler + m3 bolts + steel wire + threaded inserts | 96.36
high temp belt 2 | 85 | 1
Total: | 2092.25
30% price increase | 2719.925

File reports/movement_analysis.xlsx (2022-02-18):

X movement analysis
M_s | 0.36 | kg | Stepper motor weight
M_x | 1 | kg | X axis mass | https://www.moonsindustries.com/p/nema-17-standard-hybrid-stepper-motors/ms17hd6p4150-000004611110008904
a_max | 0.5 | m/s^2 | Max acceleration
g | 9.81 | m/s^2 | Gravity
u_bearing | 0.0015 |  | Bearing Frictional Coefficient of 608ZZ bearing | https://koyo.jtekt.co.jp/en/support/bearing-knowledge/8-4000.html
F_x | 0.5 | N | Force required to move X assembly
F_f | 0.014715 | N | Force of friction
F_total | 0.514715 | N | Total force required by X stepper motor
r_pulley | 0.0047 | m | Radius of pulley
T | 0.0024191605 | Nm | Total torque required
T_current | 0.3142 | Nm | Total torque our motor supplies
Pancacke stepper motor max speed | 180 | rpm |  | https://www.omc-stepperonline.com/nema-17-bipolar-1-8deg-16ncm-22-6oz-in-1a-3-7v-42x42x20mm-4-wires.html
Torque | 1200 | g*cm
 | 120 | Nm
 | 0.032

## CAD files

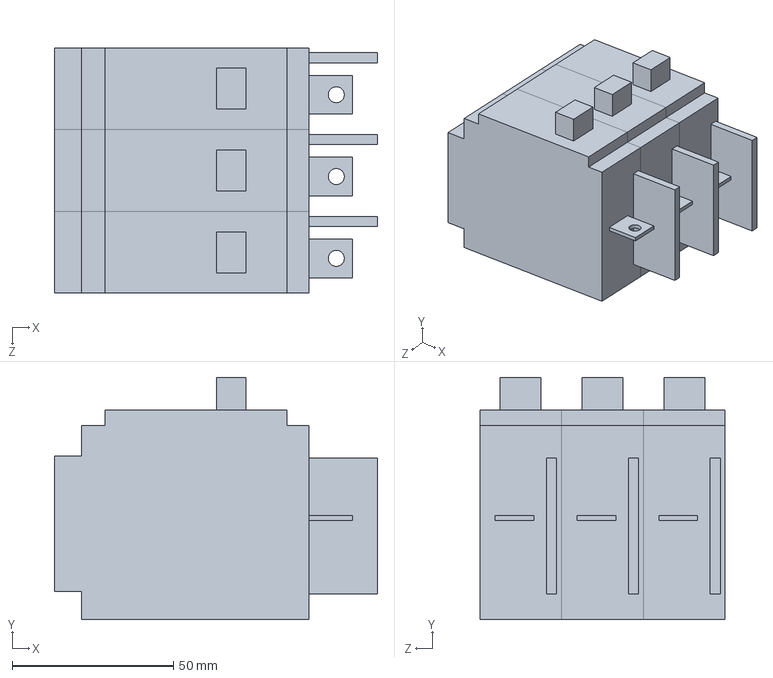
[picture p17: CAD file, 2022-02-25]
FINAL ASSEMBLY 3DPP/Breaker/Breaker.SLDASM
100.3 x 75.2 x 76.2 mm
Breaker Component x 3

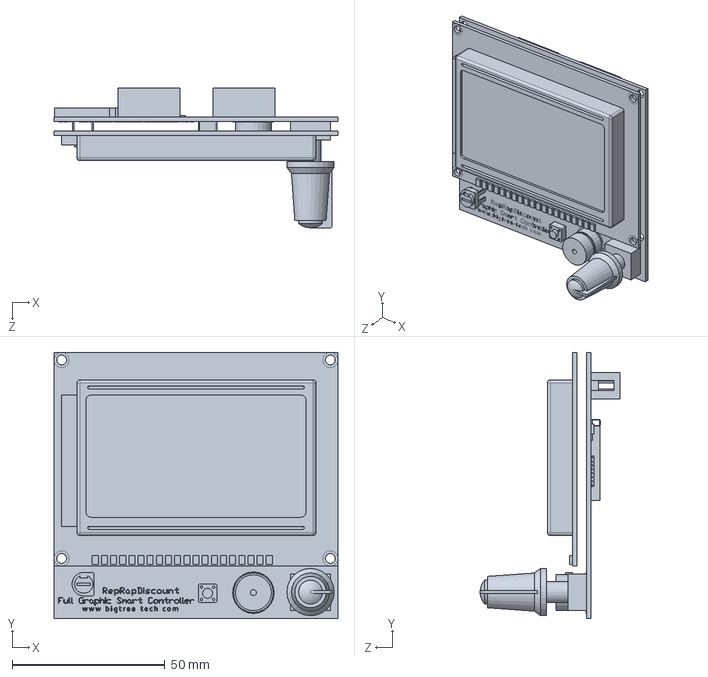
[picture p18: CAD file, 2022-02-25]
FINAL ASSEMBLY 3DPP/LCD Display/RepRapDiscount_Full Graphic Smart Controller.SLDPRT
93.0 x 87.2 x 45.8 mm

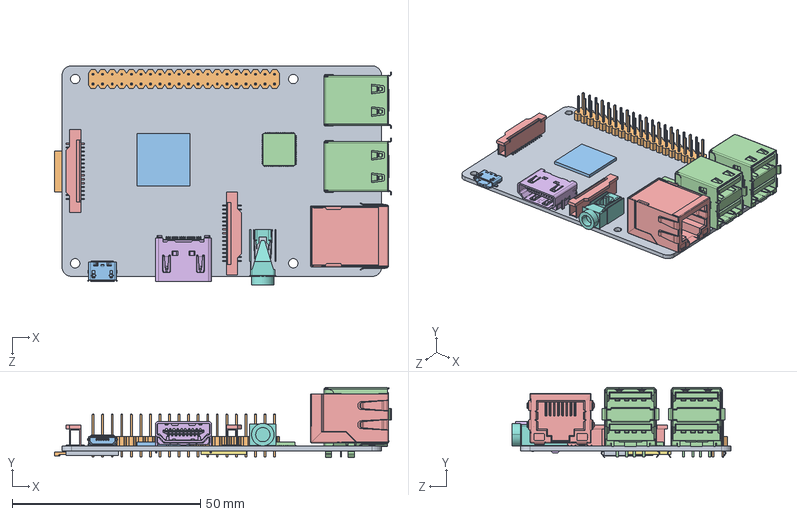
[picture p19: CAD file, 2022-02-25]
FINAL ASSEMBLY 3DPP/rpi/RaspberryPi2 STEP214.SLDASM
89.6 x 18.7 x 58.3 mm
Mainboard2.STEP
GPIO.STEP
Processor.STEP
GPU.STEP
CameraAssembly.STEP x 2
HDMI.STEP
RAM.STEP
Audio.STEP
MicroSDSocket.STEP
MicroSD.STEP
micro USB2.STEP
usb double.STEP x 2
RJ45-LED.STEP

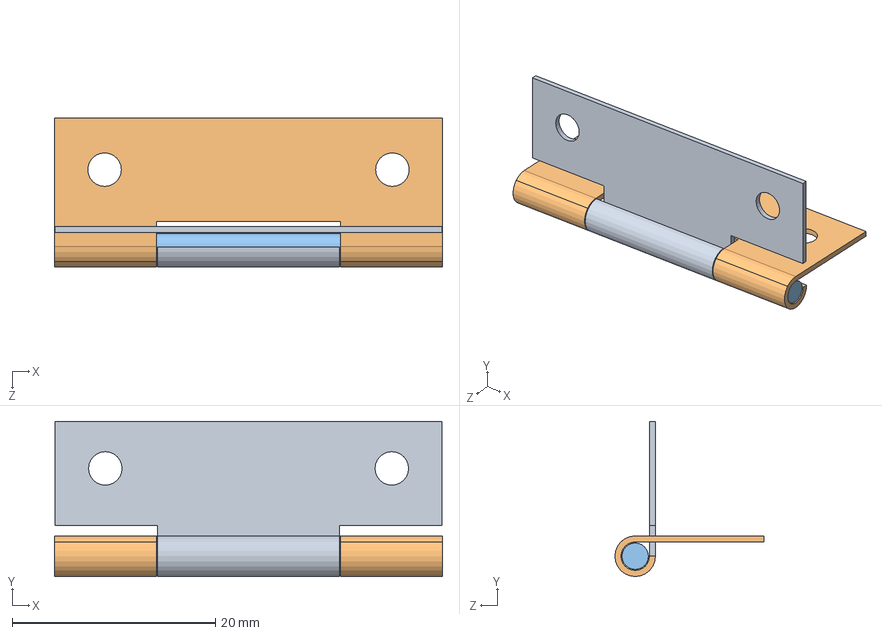
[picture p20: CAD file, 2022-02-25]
FINAL ASSEMBLY 3DPP/Small GMS Hindges/GMS Small Hindge Assembly.SLDASM
38.2 x 15.3 x 14.7 mm
GMS Hindge Small P1
GMS Hindge Small P2
GMS Hindge Small P3

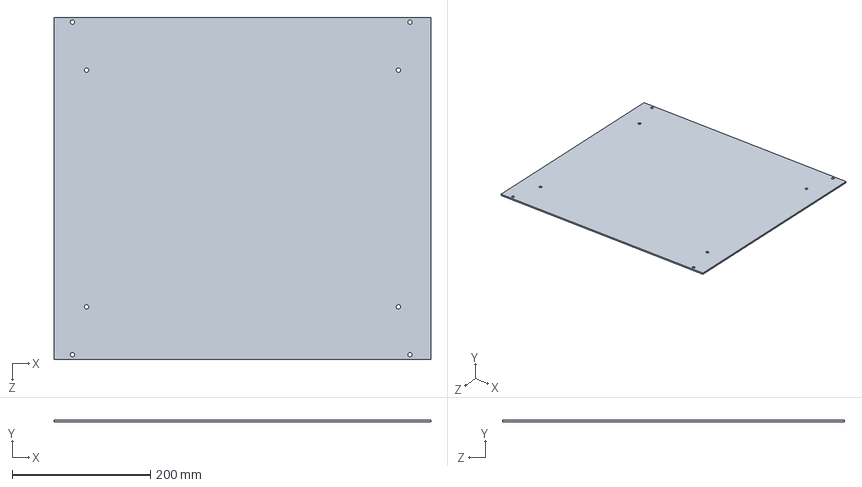
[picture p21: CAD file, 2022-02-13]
components/m3dd frame/M3DD Assembly.SLDASM
546.1 x 3.17 x 495.3 mm

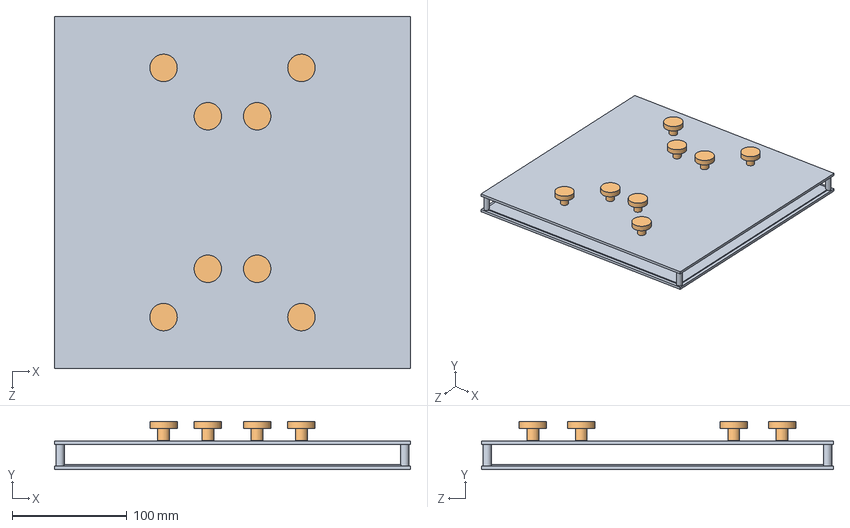
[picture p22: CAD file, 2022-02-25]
FINAL ASSEMBLY 3DPP/Heated Bed/Heated Bed Full.SLDASM
310.8 x 42.3 x 307.1 mm
Heated Bed
Rollers x 8

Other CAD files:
components/m3dd frame/FRAME/X.step.SLDASM
FINAL ASSEMBLY 3DPP/BASE FRAME FEET/Base Frame Feet Plate Assembly (3).step.SLDASM
FINAL ASSEMBLY 3DPP/FRAME/X.step.SLDASM
FINAL ASSEMBLY 3DPP/WHEEL ASSEMBLY/Roller Wheel, Bearing v4 (2).step.SLDASM
FINAL ASSEMBLY 3DPP/X AXIS/Wheel Kit - X.step.SLDASM
FINAL ASSEMBLY 3DPP/Y AXIS/Wheel Kit - Y Left Hex_1.step.SLDASM
FINAL ASSEMBLY 3DPP/Z AXIS/Z-Axis Top Bracket Assembly v7.step.SLDASM
FINAL ASSEMBLY 3DPP/BASE FRAME FEET/Base Frame Feet Plate Assembly (1).step.SLDASM
FINAL ASSEMBLY 3DPP/FRAME/CR-10S Pro Assembly.step.SLDASM
FINAL ASSEMBLY 3DPP/WHEEL ASSEMBLY/Roller Wheel, Bearing v4 (7) (1) (1)_1.step.SLDASM
FINAL ASSEMBLY 3DPP/X AXIS/X.step.SLDASM
FINAL ASSEMBLY 3DPP/Y AXIS/Y-Axis Bed Assembly v12.step.SLDASM
FINAL ASSEMBLY 3DPP/BASE FRAME FEET/Base Frame Feet Plate Assembly (2).step.SLDASM
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

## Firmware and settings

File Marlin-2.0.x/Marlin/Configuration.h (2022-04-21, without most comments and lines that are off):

#pragma once
#define CONFIGURATION_H_VERSION 02000901
#define STRING_CONFIG_H_AUTHOR "(Josh Booth, default config)" // Who made the changes.
#define SHOW_BOOTSCREEN
#define SERIAL_PORT -1
#define BAUDRATE 250000
  #define MOTHERBOARD BOARD_BTT_SKR_V2_0_REV_B
#define CUSTOM_MACHINE_NAME "3DPP"
#if LINEAR_AXES >= 4
  #define AXIS4_NAME 'A' // :['A', 'B', 'C', 'U', 'V', 'W']
#endif
#if LINEAR_AXES >= 5
  #define AXIS5_NAME 'B' // :['A', 'B', 'C', 'U', 'V', 'W']
#endif
#if LINEAR_AXES >= 6
  #define AXIS6_NAME 'C' // :['A', 'B', 'C', 'U', 'V', 'W']
#endif
#define EXTRUDERS 1
#define DEFAULT_NOMINAL_FILAMENT_DIA 1.75
#define TEMP_SENSOR_0 1047
#define TEMP_SENSOR_1 0
#define TEMP_SENSOR_2 0
#define TEMP_SENSOR_3 0
#define TEMP_SENSOR_4 0
#define TEMP_SENSOR_5 0
#define TEMP_SENSOR_6 0
#define TEMP_SENSOR_7 0
#define TEMP_SENSOR_BED 5
#define TEMP_SENSOR_PROBE 0
#define TEMP_SENSOR_CHAMBER 1
#define TEMP_SENSOR_COOLER 0
#define TEMP_SENSOR_REDUNDANT 0
#define DUMMY_THERMISTOR_998_VALUE  25
#define DUMMY_THERMISTOR_999_VALUE 100
#define TEMP_RESIDENCY_TIME         10  // (seconds) Time to wait for hotend to "settle" in M109
#define TEMP_WINDOW                  1  // (°C) Temperature proximity for the "temperature reached" timer
#define TEMP_HYSTERESIS              4  // (°C) Temperature proximity considered "close enough" to the target
#define TEMP_BED_RESIDENCY_TIME     10  // (seconds) Time to wait for bed to "settle" in M190
#define TEMP_BED_WINDOW              1  // (°C) Temperature proximity for the "temperature reached" timer
#define TEMP_BED_HYSTERESIS          3  // (°C) Temperature proximity considered "close enough" to the target
#define TEMP_CHAMBER_RESIDENCY_TIME 60  // (seconds) Time to wait for chamber to "settle" in M191
#define TEMP_CHAMBER_WINDOW          5  // (°C) Temperature proximity for the "temperature reached" timer
#define TEMP_CHAMBER_HYSTERESIS      5  // (°C) Temperature proximity considered "close enough" to the target
#if TEMP_SENSOR_REDUNDANT
  #define TEMP_SENSOR_REDUNDANT_SOURCE     1  // The sensor that will provide the redundant reading.
  #define TEMP_SENSOR_REDUNDANT_TARGET     0  // The sensor that we are providing a redundant reading for.
  #define TEMP_SENSOR_REDUNDANT_MAX_DIFF  10  // (°C) Temperature difference that will trigger a print abort.
#endif
#define HEATER_0_MINTEMP   5
#define HEATER_1_MINTEMP   5
#define HEATER_2_MINTEMP   5
#define HEATER_3_MINTEMP   5
#define HEATER_4_MINTEMP   5
#define HEATER_5_MINTEMP   5
#define HEATER_6_MINTEMP   5
#define HEATER_7_MINTEMP   5
#define BED_MINTEMP        5
#define CHAMBER_MINTEMP    5
#define HEATER_0_MAXTEMP 450
#define HEATER_1_MAXTEMP 275
#define HEATER_2_MAXTEMP 275
#define HEATER_3_MAXTEMP 275
#define HEATER_4_MAXTEMP 275
#define HEATER_5_MAXTEMP 275
#define HEATER_6_MAXTEMP 275
#define HEATER_7_MAXTEMP 275
#define BED_MAXTEMP      200
#define CHAMBER_MAXTEMP  110
#define HOTEND_OVERSHOOT 15   // (°C) Forbid temperatures over MAXTEMP - OVERSHOOT
#define BED_OVERSHOOT    10   // (°C) Forbid temperatures over MAXTEMP - OVERSHOOT
#define COOLER_OVERSHOOT  2   // (°C) Forbid temperatures closer than OVERSHOOT
#define PIDTEMP
#define BANG_MAX 255     // Limits current to nozzle while in bang-bang mode; 255=full current
#define PID_MAX BANG_MAX // Limits current to nozzle while PID is active (see PID_FUNCTIONAL_RANGE below); 255=full current
#define PID_K1 0.95      // Smoothing factor within any PID loop
    #define DEFAULT_Kp  27.55
    #define DEFAULT_Ki   2.90
    #define DEFAULT_Kd 65.40
#define PIDTEMPBED
#define MAX_BED_POWER 255 // limits duty cycle to bed; 255=full current
  #define DEFAULT_bedKp 16.52
  #define DEFAULT_bedKi 1.30
  #define DEFAULT_bedKd 140.31
#define CHAMBER_LIMIT_SWITCHING
#define MAX_CHAMBER_POWER 255 // limits duty cycle to chamber heater; 255=full current
  #define PID_FUNCTIONAL_RANGE 10 // If the temperature difference between the target temperature and the actual temperature
#define PREVENT_COLD_EXTRUSION
#define EXTRUDE_MINTEMP 170
#define PREVENT_LENGTHY_EXTRUDE
#define EXTRUDE_MAXLENGTH 200
#define THERMAL_PROTECTION_COOLER  // Enable thermal protection for the laser cooling
#define USE_XMIN_PLUG
#define USE_YMIN_PLUG
#define USE_ZMIN_PLUG
#define ENDSTOPPULLUPS
#define X_MIN_ENDSTOP_INVERTING false // Set to true to invert the logic of the endstop.
#define Y_MIN_ENDSTOP_INVERTING false // Set to true to invert the logic of the endstop.
#define Z_MIN_ENDSTOP_INVERTING false // Set to true to invert the logic of the endstop.
#define I_MIN_ENDSTOP_INVERTING false // Set to true to invert the logic of the endstop.
#define J_MIN_ENDSTOP_INVERTING false // Set to true to invert the logic of the endstop.
#define K_MIN_ENDSTOP_INVERTING false // Set to true to invert the logic of the endstop.
#define X_MAX_ENDSTOP_INVERTING false // Set to true to invert the logic of the endstop.
#define Y_MAX_ENDSTOP_INVERTING false // Set to true to invert the logic of the endstop.
#define Z_MAX_ENDSTOP_INVERTING false // Set to true to invert the logic of the endstop.
#define I_MAX_ENDSTOP_INVERTING false // Set to true to invert the logic of the endstop.
#define J_MAX_ENDSTOP_INVERTING false // Set to true to invert the logic of the endstop.
#define K_MAX_ENDSTOP_INVERTING false // Set to true to invert the logic of the endstop.
#define Z_MIN_PROBE_ENDSTOP_INVERTING false // Set to true to invert the logic of the probe.
#define X_DRIVER_TYPE  TMC2209
#define Y_DRIVER_TYPE  TMC2209
#define Z_DRIVER_TYPE  TMC2209
#define Z2_DRIVER_TYPE TMC2209
#define E0_DRIVER_TYPE TMC2209
#define ENDSTOP_NOISE_THRESHOLD 4
#define DETECT_BROKEN_ENDSTOP
#define DEFAULT_AXIS_STEPS_PER_UNIT   {80, 80, 1600, 140 }
#define DEFAULT_MAX_FEEDRATE          { 500, 500, 100, 25 }
#define DEFAULT_MAX_ACCELERATION      { 500, 500, 100, 5000 }
#define DEFAULT_ACCELERATION          500    // X, Y, Z and E acceleration for printing moves
#define DEFAULT_RETRACT_ACCELERATION  500    // E acceleration for retracts
#define DEFAULT_TRAVEL_ACCELERATION   500    // X, Y, Z acceleration for travel (non printing) moves
#define DEFAULT_EJERK    5.0  // May be used by Linear Advance
  #define JUNCTION_DEVIATION_MM 0.013 // (mm) Distance from real junction edge
  #define JD_HANDLE_SMALL_SEGMENTS    // Use curvature estimation instead of just the junction angle
#define S_CURVE_ACCELERATION
#define Z_MIN_PROBE_USES_Z_MIN_ENDSTOP_PIN
#define USE_PROBE_FOR_Z_HOMING
#define BLTOUCH
#define NOZZLE_TO_PROBE_OFFSET { -48, -10, 0 }
#define PROBING_MARGIN 15
#define XY_PROBE_FEEDRATE (133*60)
#define Z_PROBE_FEEDRATE_FAST (2*60)
#define Z_PROBE_FEEDRATE_SLOW (Z_PROBE_FEEDRATE_FAST / 1.5)
#define MULTIPLE_PROBING 2
#define Z_CLEARANCE_DEPLOY_PROBE   10 // Z Clearance for Deploy/Stow
#define Z_CLEARANCE_BETWEEN_PROBES  5 // Z Clearance between probe points
#define Z_CLEARANCE_MULTI_PROBE     5 // Z Clearance between multiple probes
#define Z_PROBE_LOW_POINT          -3 // Farthest distance below the trigger-point to go before stopping
#define Z_PROBE_OFFSET_RANGE_MIN -20
#define Z_PROBE_OFFSET_RANGE_MAX 20
#define Z_MIN_PROBE_REPEATABILITY_TEST
#define X_ENABLE_ON 0
#define Y_ENABLE_ON 0
#define Z_ENABLE_ON 0
#define E_ENABLE_ON 0 // For all extruders
#define DISABLE_X false
#define DISABLE_Y false
#define DISABLE_Z false
#define DISABLE_E false             // Disable the extruder when not stepping
#define DISABLE_INACTIVE_EXTRUDER   // Keep only the active extruder enabled
#define INVERT_X_DIR true
#define INVERT_Y_DIR true
#define INVERT_Z_DIR true
#define INVERT_E0_DIR true
#define INVERT_E1_DIR false
#define INVERT_E2_DIR false
#define INVERT_E3_DIR false
#define INVERT_E4_DIR false
#define INVERT_E5_DIR false
#define INVERT_E6_DIR false
#define INVERT_E7_DIR false
#define X_HOME_DIR -1
#define Y_HOME_DIR -1
#define Z_HOME_DIR -1
#define X_BED_SIZE 300
#define Y_BED_SIZE 280
#define X_MIN_POS 0
#define Y_MIN_POS 0
#define Z_MIN_POS 0
#define X_MAX_POS X_BED_SIZE
#define Y_MAX_POS Y_BED_SIZE
#define Z_MAX_POS 1330
#define MIN_SOFTWARE_ENDSTOPS
  #define MIN_SOFTWARE_ENDSTOP_X
  #define MIN_SOFTWARE_ENDSTOP_Y
  #define MIN_SOFTWARE_ENDSTOP_Z
  #define MIN_SOFTWARE_ENDSTOP_I
  #define MIN_SOFTWARE_ENDSTOP_J
  #define MIN_SOFTWARE_ENDSTOP_K
#define MAX_SOFTWARE_ENDSTOPS
  #define MAX_SOFTWARE_ENDSTOP_X
  #define MAX_SOFTWARE_ENDSTOP_Y
  #define MAX_SOFTWARE_ENDSTOP_Z
  #define MAX_SOFTWARE_ENDSTOP_I
  #define MAX_SOFTWARE_ENDSTOP_J
  #define MAX_SOFTWARE_ENDSTOP_K
#define AUTO_BED_LEVELING_BILINEAR
#define ENABLE_LEVELING_AFTER_G28
#define PREHEAT_BEFORE_LEVELING
  #define LEVELING_NOZZLE_TEMP 180   // (°C) Only applies to E0 at this time
  #define LEVELING_BED_TEMP     60
#define DEBUG_LEVELING_FEATURE
  #define ENABLE_LEVELING_FADE_HEIGHT
    #define DEFAULT_LEVELING_FADE_HEIGHT 5.0 // (mm) Default fade height.
  #define SEGMENT_LEVELED_MOVES
  #define LEVELED_SEGMENT_LENGTH 5.0 // (mm) Length of all segments (except the last one)
  #define GRID_MAX_POINTS_X 5
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

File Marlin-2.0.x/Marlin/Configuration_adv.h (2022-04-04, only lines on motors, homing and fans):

#define E0_AUTO_FAN_PIN -1
#define E1_AUTO_FAN_PIN -1
#define E2_AUTO_FAN_PIN -1
#define E3_AUTO_FAN_PIN -1
#define E4_AUTO_FAN_PIN -1
#define E5_AUTO_FAN_PIN -1
#define E6_AUTO_FAN_PIN -1
#define E7_AUTO_FAN_PIN -1
#define CHAMBER_AUTO_FAN_PIN -1
#define COOLER_AUTO_FAN_PIN -1
#define COOLER_FAN_PIN -1
#define HOMING_BUMP_MM      { 5, 5, 2 }       // (mm) Backoff from endstops after first bump
#define HOMING_BUMP_DIVISOR { 2, 2, 4 }       // Re-Bump Speed Divisor (Divides the Homing Feedrate)
  #define HOME_AFTER_G34
#define MICROSTEP_MODES { 16, 16, 16, 16, 16, 16 } // [1,2,4,8,16]
#define ADVANCED_PAUSE_FEATURE
  #define ADVANCED_PAUSE_PURGE_FEEDRATE        3  // (mm/s) Extrude feedrate (after loading). Should be slower than load feedrate.
  #define ADVANCED_PAUSE_PURGE_LENGTH         50  // (mm) Length to extrude after loading.
  #define ADVANCED_PAUSE_RESUME_PRIME          0  // (mm) Extra distance to prime nozzle after returning from park.
    #define X_CURRENT       800        // (mA) RMS current. Multiply by 1.414 for peak current.
    #define X_CURRENT_HOME  X_CURRENT  // (mA) RMS current for sensorless homing
    #define X_MICROSTEPS     16        // 0..256
    #define Y_CURRENT       800
    #define Y_CURRENT_HOME  Y_CURRENT
    #define Y_MICROSTEPS     16
    #define Z_CURRENT       800
    #define Z_CURRENT_HOME  Z_CURRENT
    #define Z_MICROSTEPS     16
    #define Z2_CURRENT      800
    #define Z2_CURRENT_HOME Z2_CURRENT
    #define Z2_MICROSTEPS    Z_MICROSTEPS
    #define E0_CURRENT      800
    #define E0_MICROSTEPS    16
    #define CURRENT_STEP_DOWN     50  // [mA]
    #define REPORT_CURRENT_CHANGE
  #define X_HYBRID_THRESHOLD     100  // [mm/s]
  #define X2_HYBRID_THRESHOLD    100
  #define Y_HYBRID_THRESHOLD     100
  #define Y2_HYBRID_THRESHOLD    100
  #define Z_HYBRID_THRESHOLD       3
  #define Z2_HYBRID_THRESHOLD      3
  #define Z3_HYBRID_THRESHOLD      3
  #define Z4_HYBRID_THRESHOLD      3
  #define I_HYBRID_THRESHOLD       3
  #define J_HYBRID_THRESHOLD       3
  #define K_HYBRID_THRESHOLD       3
  #define E0_HYBRID_THRESHOLD     30
  #define E1_HYBRID_THRESHOLD     30
  #define E2_HYBRID_THRESHOLD     30
  #define E3_HYBRID_THRESHOLD     30
  #define E4_HYBRID_THRESHOLD     30
  #define E5_HYBRID_THRESHOLD     30
  #define E6_HYBRID_THRESHOLD     30
  #define E7_HYBRID_THRESHOLD     30

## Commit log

2022-02-03 added SKR board
    [PRINTER.DSN]
2022-02-04 added rpi
    [PRINTER.DSN, raspberry-pi-3-b-plus-mechanical-drawing.dxf]
2022-02-04 created parts and assembly for frame
    [Assem1.SLDASM, M3DD Assembly.SLDASM, angle with holes.SLDPRT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]
2022-02-04 updated SKR and related schematics
    [PRINTER.DSN]
2022-02-07 finished schematics
    [PRINTER.DSN]
2022-02-07 added budget
    [preliminary_budget.xlsx]
2022-02-07 Added LCD Display and Rpi
    [RepRapDiscount_Full Graphic Smart Controller.SLDPRT, raspberry-pi-3-b-plus-mechanical-drawing.dxf]
2022-02-07 Created buck converter
    [Buck Converter 1.SLDPRT]
2022-02-10 Added more parts to assembly including crossbeam bottom, mounting plate 2, and mounting plate 3
    [M3DD Assembly.SLDASM, crossbeam bottom.SLDPRT, crossbeam top.SLDPRT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]
2022-02-13 post cadfest
    [Breaker Component.SLDPRT, Breaker.SLDASM, Buck Converter 1.SLDPRT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]
2022-02-14 updated prelim design report
    [existing solutions analysis.xlsx]
2022-02-15 got report back to where it was
    [existing solutions analysis.xlsx, power_analysis.xlsx, prelim_thermal_analysis.xlsx]
2022-02-15 lowered font size to 11
    [preliminary_budget.xlsx]
2022-02-15 moved budget into reports
    [preliminary_budget.xlsx]
2022-02-15 working version of powerpoint
2022-02-16 tuesday work session
    [prelim_thermal_analysis.xlsx]
2022-02-18 added theme
    [movement_analysis.xlsx]
2022-02-25 case finished
    [1001-3.step.SLDPRT, 1001-4.step.SLDPRT, 1001-5.step.SLDPRT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]
2022-02-28 added final budget
    [final_budget.xlsx]
2022-04-04 added marlin
    [20x24 sheet metal.SLDPRT, Assem2.SLDASM, Breaker Base Plate.SLDPRT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]
2022-04-21 CAD model finished
    [1001-3.step.SLDPRT, 1001-4.step.SLDPRT, 1001-5.step.SLDPRT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]

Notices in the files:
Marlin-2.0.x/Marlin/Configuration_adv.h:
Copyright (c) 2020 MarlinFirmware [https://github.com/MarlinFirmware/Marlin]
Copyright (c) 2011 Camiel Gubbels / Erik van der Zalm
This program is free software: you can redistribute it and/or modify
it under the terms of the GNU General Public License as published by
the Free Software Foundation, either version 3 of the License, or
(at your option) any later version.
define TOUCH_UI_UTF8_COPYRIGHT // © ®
